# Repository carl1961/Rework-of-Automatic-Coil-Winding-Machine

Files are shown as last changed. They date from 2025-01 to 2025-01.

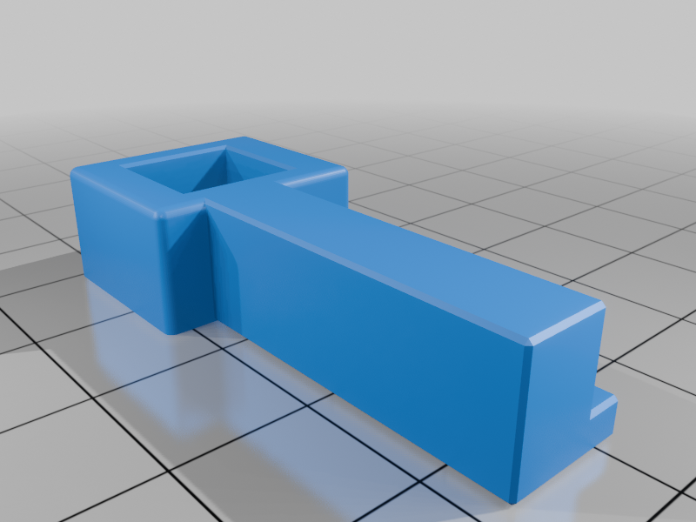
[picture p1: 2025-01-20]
images/Wire_Guide_Feeder-Mount.png

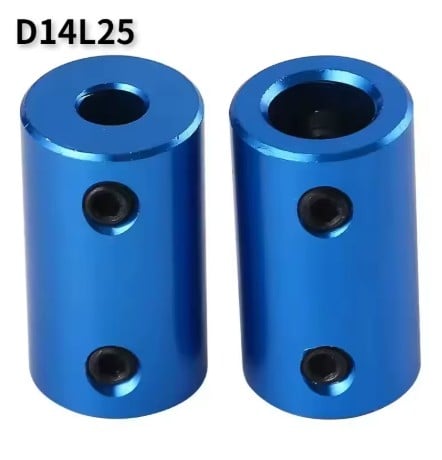
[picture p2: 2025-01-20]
images/Screenshot_2025-01-19_011432.jpg

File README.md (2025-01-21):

# Rework-of-Automatic-Coil-Winding-Machine
Rework of HyperspacePirate, GREAT!  Automatic Coil Winding Machine

MGN9 Linear Rail 
!!! Always check here before 3D Printing, I always update fixes and support !!!

Running ContosChaos GREAT! Firmware, Be sure to thank him.       https://www.thingiverse.com/thing:6619123
changed pins to use a MKS DLC 2.0  (Firmware in downloads)

coming soon....    Arduino Uno CNC Shield  KeyeStudio Nano CNC Shield 2016, yellow and black  ( Never use the red clone 2014 Version on Ali express, Ebay or Amazon, they have the stepper Jumpers going to ground, the jumper or useless. search Nano CNC shield and you will find why).

Added parts I work with to create electromagnet coils.
Step files. For Fusion360 files, get from here https://www.thingiverse.com/thing:6918293/files

MGN9 Linear Rail     https://www.aliexpress.us/w/wholesale-MG9-H-250mm-Linear-Rail.html?spm=a2g0o.productlist.search.0    https://www.aliexpress.us/item/3256807753002598.html
Bearings used is:
608Z 22mmOD x8mm ID for Pillow Block    https://www.aliexpress.us/w/wholesale-608Z.html?spm=a2g0o.productlist.search.0
625Z  16mm OD x 5mm ID for Rotor               https://www.aliexpress.us/w/wholesale-625Z.html?spm=a2g0o.productlist.search.0
These bearings  and the shaft came out of a old nema 17 stepper motor, their is also a 3D print part Bearing_Block_13mm-OD-5mmID_Bearing if you have the 695Z 13mm OD x 5mm ID

695Z   https://www.aliexpress.us/w/wholesale-695Z.html?spm=a2g0o.productlist.search.0

Limit Switches used
1 Horizontal Type Mechanical Endstop  https://www.aliexpress.us/w/wholesale-Horizontal-Type-Mechanical-Endstop.html?spm=a2g0o.productlist.search.0
1 Vertical  Type Mechanical Endstop      https://www.aliexpress.us/w/wholesale-Vertical-Type-Mechanical-Endstop.html?spm=a2g0o.detail.search.0

4 M3 Thumb Nuts  , Limit switches and threader parts  https://www.aliexpress.us/w/wholesale-M3-thumb-Nuts.html?spm=a2g0o.productlist.search.0
You want the thumb nuts that or threaded all the way.  exmple:  https://www.aliexpress.us/item/3256803754283283.html

5mmx8mm Shaft Coupler  (Solidn no Flex)  https://www.aliexpress.us/w/wholesale-5mmx8mm-Shaft-Coupler.html?spm=a2g0o.store_pc_home.search.0
6x6x6mm button   https://www.aliexpress.us/w/wholesale-6x6x6mm-button.html?spm=a2g0o.store_pc_home.search.0
1602  LCD  I2C      https://www.aliexpress.us/w/wholesale-1602--LCD--I2C.html?spm=a2g0o.detail.search.0
MKS DLC 2.0 / MKS DLC V2.1 (Uno on board)  https://www.aliexpress.us/w/wholesale-MKS-DLC-V2.1.html?spm=a2g0o.detail.search.0
Example:  https://www.aliexpress.us/item/2251832727498645.html

Update: 1-20-25
Right EndStop Switch Mount,  Redone to reach Right side of Spool.
Step and Fusion360 files

Update: 1/19/25
Left EndStop Switch Mount,  Redone to reach Left side of Spool.
Updated case's, button holes repositioned for 2.54 spacing.
Push button mounts, one for PCB and the other for buttons only (soldering wires to button)
Wire rod mount with M5 nut to secure M8 round rod.
Screw holes for console base plate (No glue needed)

Menu on LCD:
14                 Left and Right button to increase or decrease Enter to except (middle button)

Wire SWG Guage:        British Standard Wire Gauge  
SWG	(in)	(mm)	 
 
14	0.080	2.032	 
15	0.072	1.829
16	0.064	1.626
17	0.056	1.422
18	0.048	1.219
19	0.040	1.016	 
20	0.036	0.914
21	0.032	0.813
22	0.028	0.711
23	0.024	0.610	 
24	0.022	0.559
25	0.020	0.5080
26	0.018	0.4572	 
27	0.0164	0.4166
28	0.0148	0.3759	 
29	0.0136	0.3454
30	0.0124	0.3150	 
31	0.0116	0.2946
32	0.0108	0.2743
33	0.0100	0.2540
34	0.0092	0.2337
35	0.0084	0.2134
36	0.0076	0.1930
37	0.0068	0.1727
38	0.0060	0.1524
39	0.0052	0.1321	 
40	0.0048	0.1219
41	0.0044	0.1118
42	0.004	0.1016
43	0.0036	0.0914
44	0.0032	0.0813
45	0.0028	0.0711
46	0.0024	0.0610
47	0.0020	0.0508
48	0.0016	0.0406
49	0.0012	0.0305	 
50	0.0010	0.0254

Number of Turns: 
100 | 2m15s              Left and Right button to increase or decrease Enter to except (middle button)

Length in mm:
162.80                       Left and Right button to increase or decrease Enter to except (middle button)

100 turns | 14SWD
162.80mm  | OK?   Left and Right button to increase or decrease Enter to except (middle button)

Move Head, use
< and >  , |->           Left and Right button to Jog   Wire_Guide_Feeder   Enter to except (middle button) (Jog to Left EndStop)

Winding 
Starting Coil
Winding In 
progress ....  Moves back ant forth using EndStops to reverse.

#First Good Run

first run
More tweaking the endstops to get rid of over run.

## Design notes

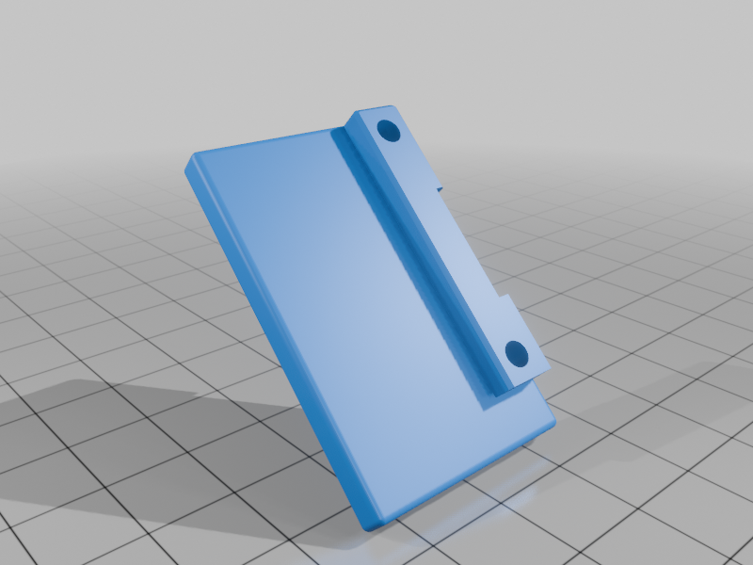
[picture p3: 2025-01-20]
images/Button_PCB_Support.png

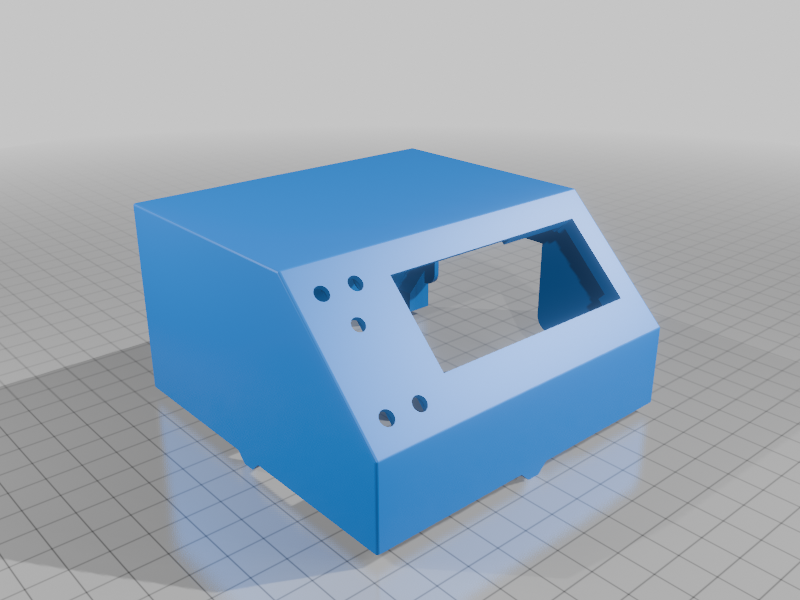
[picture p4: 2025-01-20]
images/Console_Case_Beveled_27mm_LCD.png

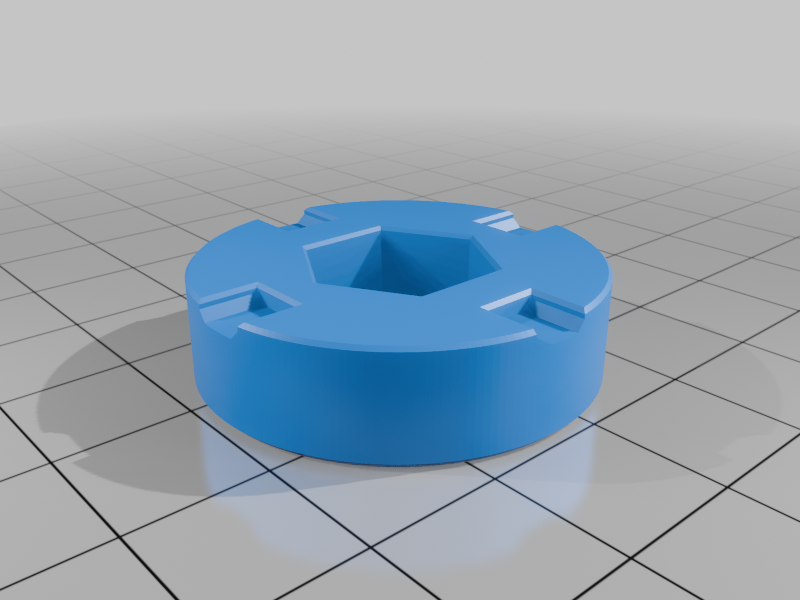
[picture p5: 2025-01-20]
images/New_Rotor_Spool_Mount_M8_Hex_Bolt_1mm_Core.png

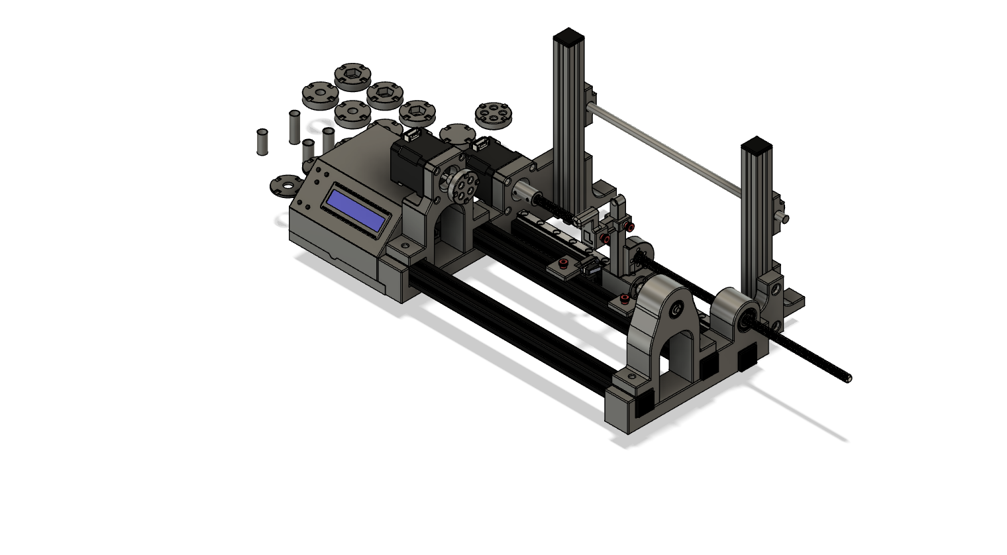
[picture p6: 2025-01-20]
images/Automatic_Coil_Winding_Machine_v32.png

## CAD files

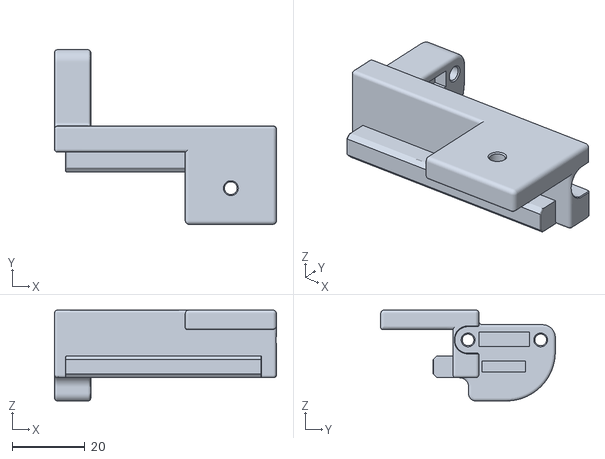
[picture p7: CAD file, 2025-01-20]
files/Left_EndStop_Switch_Mount_Longer.stl
61.1 x 48.1 x 25.0

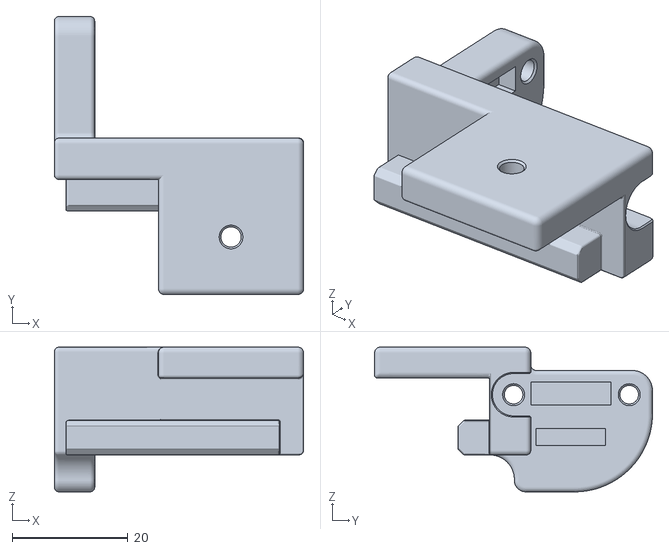
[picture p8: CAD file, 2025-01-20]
files/Left_EndStop_Switch_Mount.stl
43.1 x 48.1 x 25.0

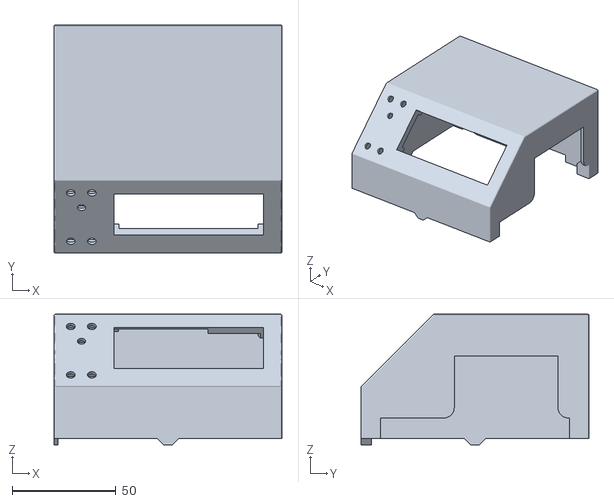
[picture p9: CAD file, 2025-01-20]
files/Console_Case_Beveled_27mm_LCD.stl
110.0 x 110.2 x 63.1

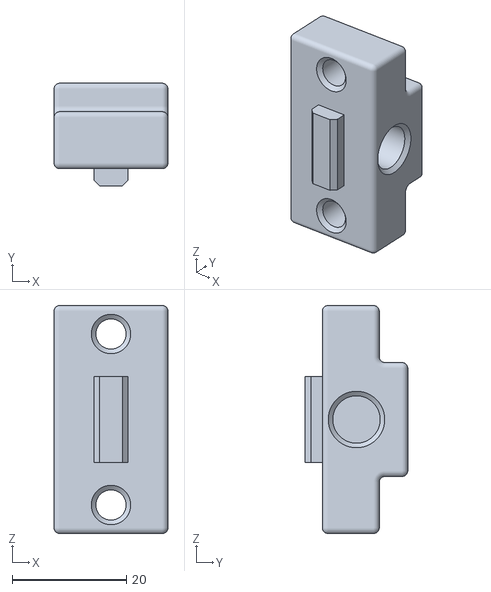
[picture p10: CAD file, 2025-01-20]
files/Wire_Spool_Rail_Block.stl
20.0 x 18.0 x 40.0

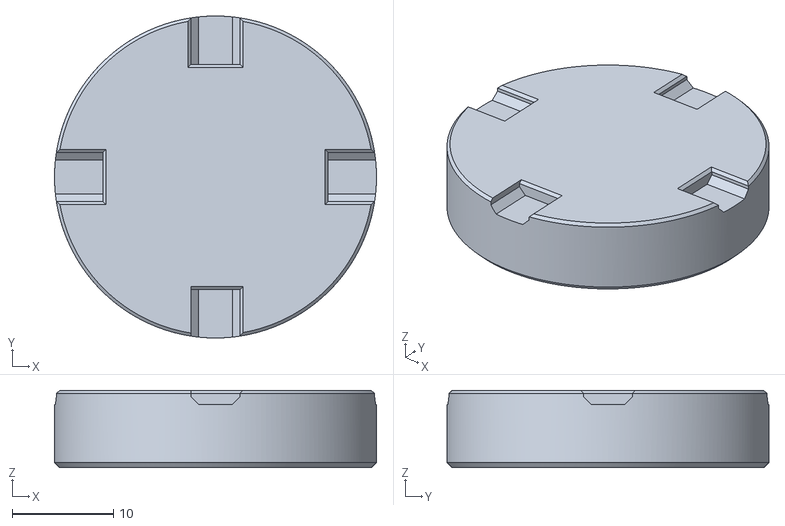
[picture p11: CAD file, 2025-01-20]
files/New_Rotor_Spool_Mount.stl
31.8 x 31.7 x 7.62

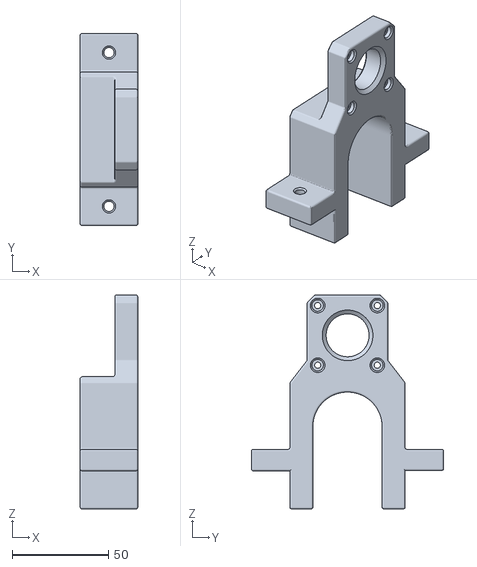
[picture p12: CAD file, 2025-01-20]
files/Stepper_Block_V2.STL
30.0 x 100.0 x 111.3

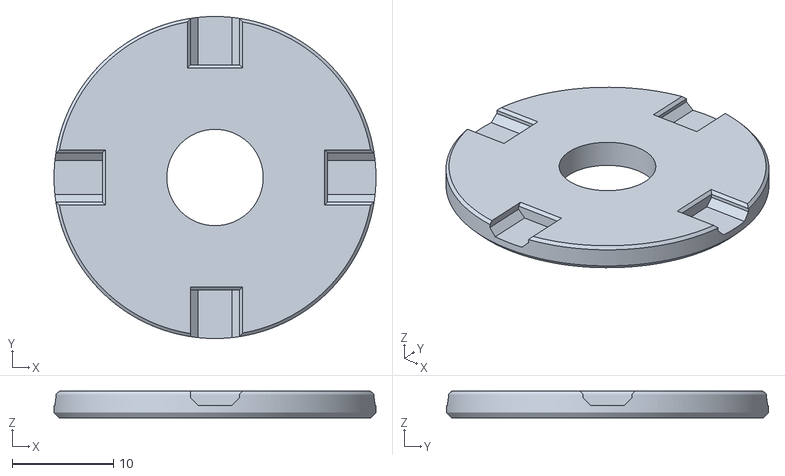
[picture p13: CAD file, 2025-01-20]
files/New_Rotor_Spool_Mount_Thin_M8_1mmCore.stl
31.7 x 31.7 x 2.62

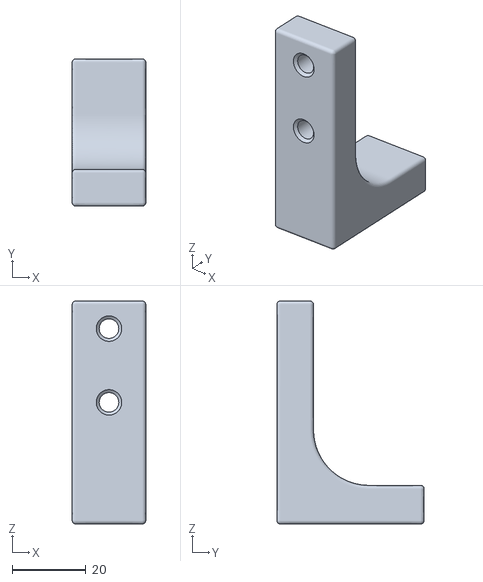
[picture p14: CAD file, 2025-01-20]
files/Balance_Foot.stl
20.0 x 40.0 x 60.5

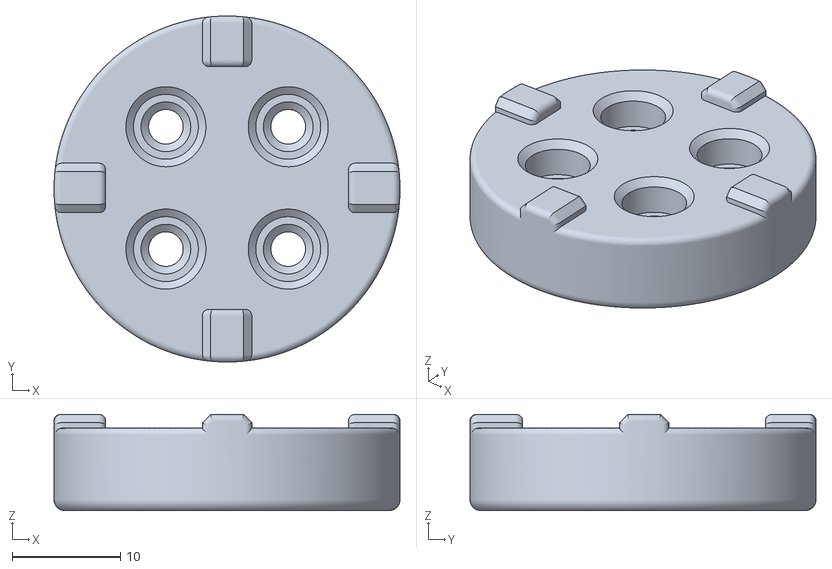
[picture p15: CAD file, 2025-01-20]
files/New_Rotor.stl
32.0 x 32.0 x 8.89

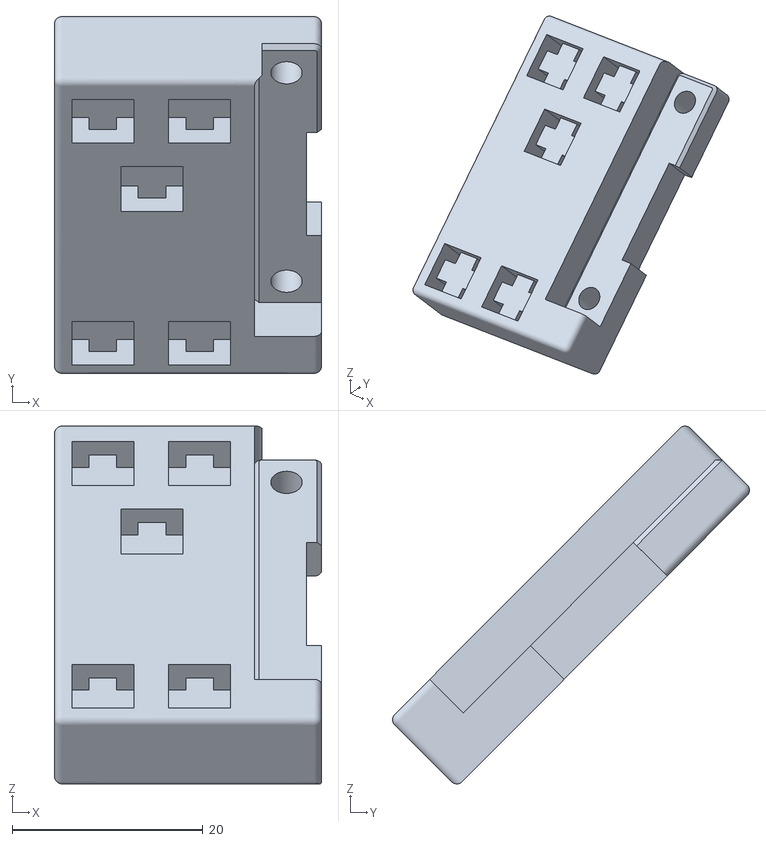
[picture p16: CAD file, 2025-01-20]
files/Button_Only_Support.stl
28.1 x 37.5 x 37.6

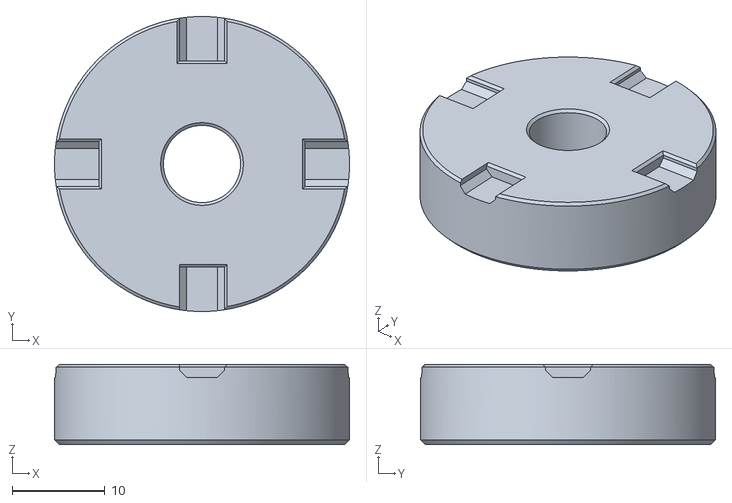
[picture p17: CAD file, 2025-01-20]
files/New_Rotor_Spool_Mount_M8_Hole_.5mm_Core.stl
31.7 x 31.7 x 8.62

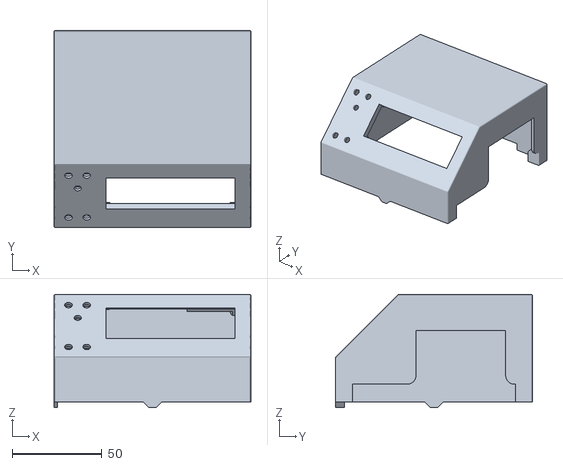
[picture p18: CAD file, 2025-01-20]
files/Console_Case_Beveled_24mm_LCD.stl
110.0 x 110.2 x 63.1

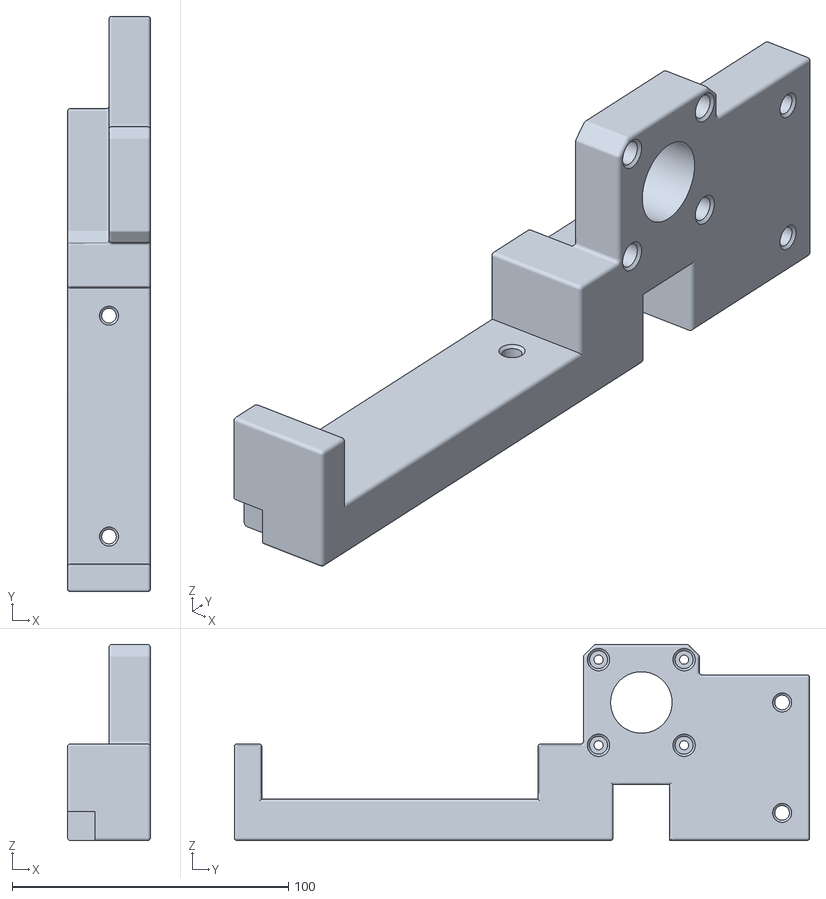
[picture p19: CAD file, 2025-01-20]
files/Bottom_Bracket_B.stl
30.0 x 208.5 x 71.0

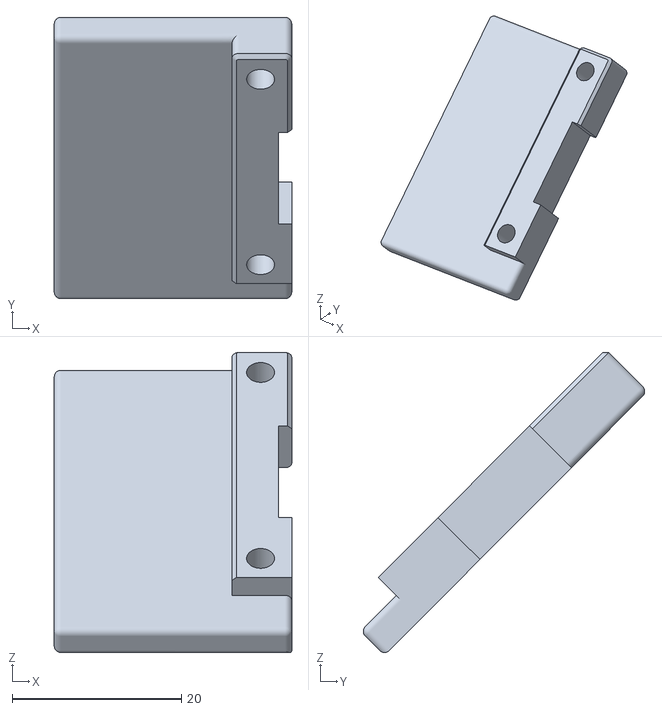
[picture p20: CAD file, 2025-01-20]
files/Button_PCB_Support.stl
28.1 x 33.2 x 35.4

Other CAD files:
files/New_Rotor_Spool_Mount_Thin_M8_Hole.stl
files/New_Rotor_Spool_Mount_M3_Hole.stl
files/Bearing_Block_16mm-OD-5mmID_Bearing.stl
files/Right_EndStop_Switch_Mount.stl
files/2020_Cap.stl
files/Base_Plate_Screw_Holes.stl
files/Bearing_Block_13mm-OD-5mmID_Bearing.stl
files/Console_Case.stl
files/Console_Case_Beveled_24mm_LCD_MKS_DLC_2.0.stl
files/M8_22_.5mm_Core.stl
files/M8_22_1mm_Core.stl
files/M8_30_.5mm_Core.stl
files/M8_30_1mm_Core.stl
files/New_Rotor_Spool_Mount_M8_Hex_Bolt.stl
files/New_Rotor_Spool_Mount_M8_Hex_Bolt_.5mm_Core.stl
files/New_Rotor_Spool_Mount_M8_Hex_Bolt_1mm_Core.stl
files/New_Rotor_Spool_Mount_M8_Hole.stl
files/New_Rotor_Spool_Mount_M8_Hole_1mm_Core.stl
files/New_Rotor_Spool_Mount_Thin_M8_.5mmCore.stl
files/Rail_Rider_MG9_Rail.stl
files/Wire_Guide_Feeder-Mount.stl
files/Wire_Spool_Rail_Block_M5_Nut.stl
